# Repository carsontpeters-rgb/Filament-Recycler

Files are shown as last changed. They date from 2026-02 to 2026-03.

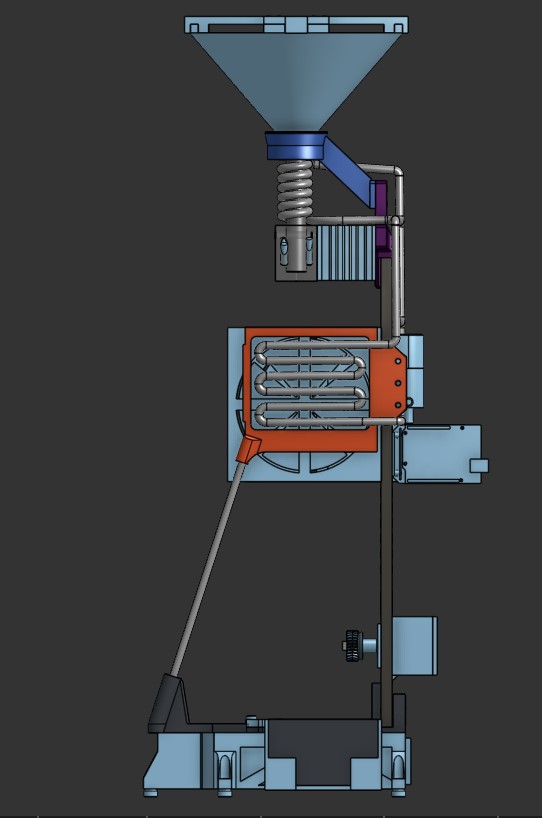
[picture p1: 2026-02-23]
Pictures/Assembly 3.jpg

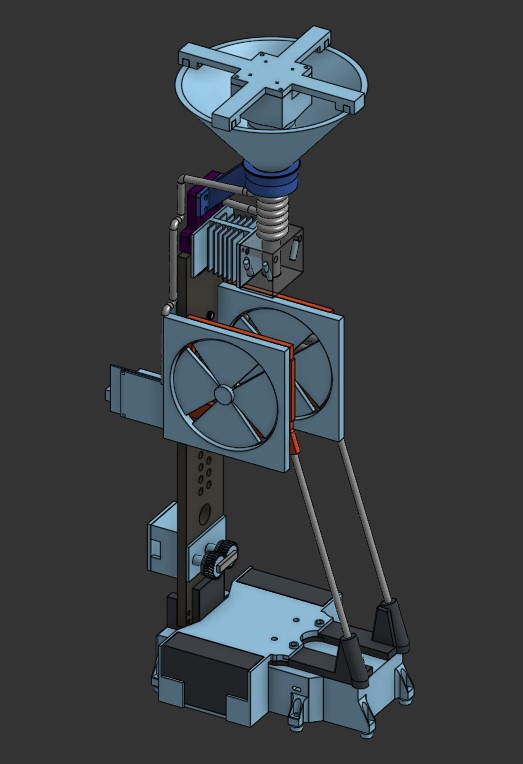
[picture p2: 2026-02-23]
Pictures/Assembly 1.jpg

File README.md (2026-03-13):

PLA Filament Recycler & Extruder
I got tired of throwing away failed prints and scraps of PLA, so I designed a machine that can recycle those scraps and turn them back into usable filament. You can also use raw PLA pellets as a material, which is much cheaper than buying a spool. Everything was designed from scratch, including the CAD, electronics, and code.
What it does
The machine takes in shredded 3D print scraps or raw PLA pellets, melts them down, and extrudes new 1.75mm filament. You can use this to recycle failed prints or support material and turn them back into usable filament. I designed this machine to save money and reduce waste from scraps of PLA I had already paid for.
How to use it

Shred old prints into small chips, or better yet, just use raw pellets. Put these into the top funnel.
Plug it in and it will automatically heat up to 210°C.
The plastic is pushed through a water-cooled steel barrel by an auger into the hot end. Melted plastic is pushed out through a 1.72mm nozzle.
Two 120mm fans cool the filament just after it exits the nozzle.
It is cooled again on its way to the spool via a stepper-driven puller, which regulates the filament diameter.
Spool it up by hand.

How it works
Feeding
Plastic goes into a hopper and gets pushed through a steel barrel by an auger. The barrel is water-cooled so that the plastic frame won't melt.
Heating
The hot end has two 12V cartridge heaters sitting in a custom-made heater block. Temperatures are monitored in real time by K-type thermocouples, which the firmware uses to maintain a constant 210°C.
Cooling & Diameter
The filament is rapidly cooled by two 120mm fans directly after exiting the nozzle. The stepper puller controls the filament diameter by varying the speed at which it pulls the filament away from the nozzle — the faster it pulls, the thinner the filament gets. You then spool it up by hand.

CAD File Notes
In the CAD file there are folders named parts, electronics, and non-printed parts. The parts folder contains everything I'll be 3D printing. The electronics folder has STEP files of all the electronics. The non-printed parts I'll either fabricate myself, have CNC'd, or purchase. Here is the link to the OnShape file https://cad.onshape.com/documents/712a637f79dd720bf38c4e9e/w/a795a65476a95b8c58273d13/e/a84f1c8939a0f9925b142090
the code was uploded using arduino ide to a arduino uno r3

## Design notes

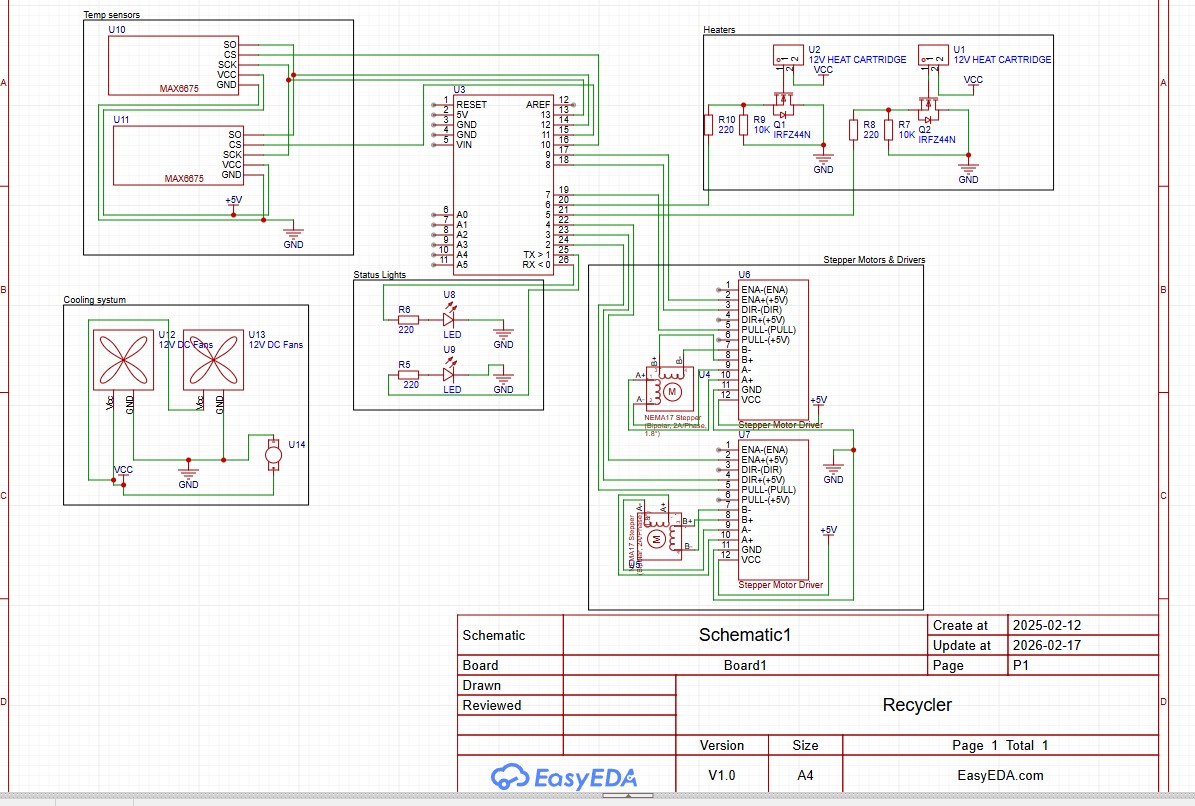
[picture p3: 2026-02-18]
Pictures/Schematic.jpg

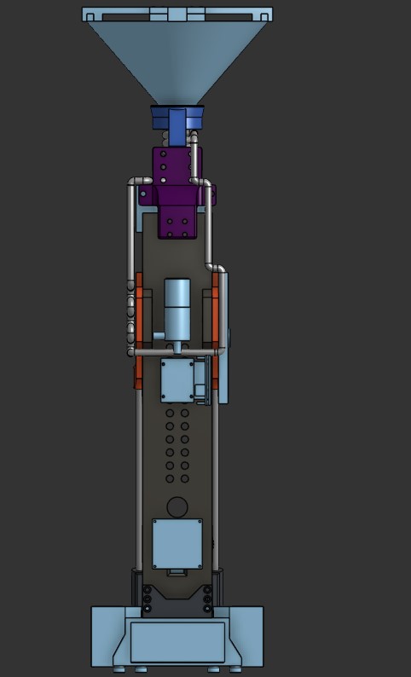
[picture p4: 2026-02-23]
Pictures/Screenshot 2026-02-23 073450.jpg

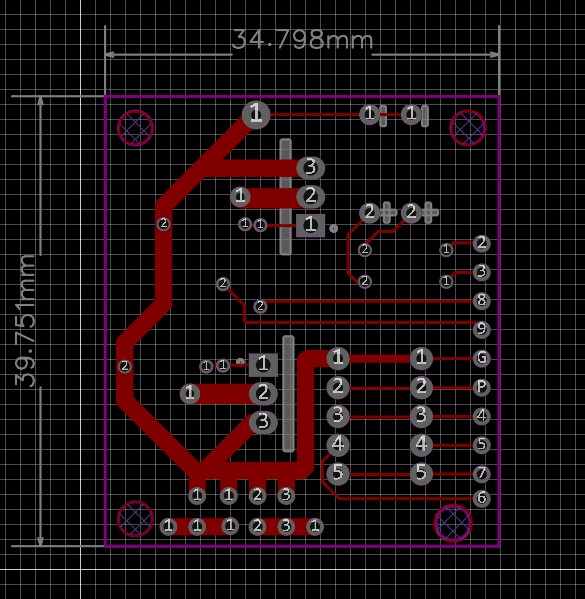
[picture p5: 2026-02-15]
Pictures/PCB.jpg

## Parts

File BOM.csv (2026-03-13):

Item Name | Description | Quantity | Unit Price | Total Price | URL | Total with tax
120mm Fan | Cooling fan for radiator | 2 | $9.89 | $19.78 | https://www.amazon.ca/gp/product/B002YFP8BK/ref=ox_sc_act_image_5?smid=A1W36NGWLHYVQ3 | $21.15
304 Stainless steel Pipe | Feed neck | 1 | $35.22 | $35.22 | https://www.amazon.ca/gp/product/B0CWY62TWC/ref=ox_sc_act_image_2?smid=A2NJO87SRDLPUU&psc=1 | $39.45
6mm Steel rod | Structual support rods | 1 | $6.79 | $6.79 | https://www.amazon.ca/gp/product/B0BDZ2VSCC/ref=ox_sc_act_image_3?smid=A2U2IW4XM8RL4X&psc=1 | $7.60
AC 110V - 220V TO DC | Power Supply | 1 | $20.95 | $20.95 | https://www.amazon.ca/gp/product/B010CVIWBK/ref=ewc_pr_img_1?smid=A2Z1VP11ZHYN88&psc=1 | $23.46
Aluminum SSR Heatsink | Heatsink | 1 | $13.49 | $13.49 | https://www.amazon.ca/gp/product/B07B3Y2ZNY/ref=ox_sc_act_image_8?smid=A35AFW9EVJYR0N&psc=1 | $15.11
Auger Drill Bit | Feed Auger | 1 | $19.45 | $19.45 | https://www.amazon.ca/gp/product/B0FSYZNZVQ/ref=ox_sc_act_image_12?smid=A2Y9NNYJ4PYMHW | $21.78
Copper round tube | For watercooling system | 1 | $15.69 | $15.69 | https://www.amazon.ca/gp/product/B09MK7HR1V/ref=ox_sc_act_image_1?smid=A30WUG2ZDGM0XM&psc=1 | $17.57
High Temperature Polyimide Tape | Heat shielding tape | 1 | $14.99 | $14.99 | https://www.amazon.ca/gp/product/B0D979ZV7G/ref=ox_sc_act_image_11?smid=ABKR4BJYL11O&psc=1 | $16.79
IRFZ44N Mosfets | Mosfets | 1 | $3.11 | $6.22 | https://www.amazon.ca/gp/product/B07PKDV4JH/ref=ox_sc_act_image_4?smid=A14A2SS3D2OXQ9&psc=1 | $6.97
MAX6675 Module | Heat sensors | 2 | $4.75 | $9.49 | https://www.amazon.ca/gp/product/B0C6QTL5Y3/ref=ox_sc_act_image_6?smid=A1VTL661FOEJB1&psc=1 | $10.63
NEMA17 Stepper Motor | Stepper motors | 2 | $9.00 | $18.00 | https://www.amazon.ca/gp/product/B0B1Q4CF87/ref=ox_sc_act_image_9?smid=A2GRTMR8P2IKL2&psc=1 | $20.16
Power Cord | cable to plug the psu in | 1 | $5.99 | $5.99 | https://www.amazon.ca/gp/product/B07BQCMPF2/ref=ox_sc_act_image_7?smid=A3DWYIK6Y9EEQB | $6.71
TB6600 Stepper Motor Driver | Stepper motor drivers | 2 | $21.36 | $42.72 | https://www.amazon.ca/gp/product/B07Z4YQ7CY/ref=ox_sc_act_image_10?smid=A22JVY9MHCKXI0&psc=1 | $47.85
Arduino Uno R3 | Micro Controller | 1 | $21.99 | $21.99 | https://www.amazon.ca/Elegoo-Board-ATmega328P-ATMEGA16U2-Arduino/dp/B01EWOE0UU?s=industrial | $24.63
Led | Lights | 2 | $2.19 | $4.38 | https://www.amazon.ca/Novelty-Place-Colors-Yellow-Lights/dp/B086V2M2TT/ref=sr_1_8?sr=8-8 | $4.91
Resitors | resitors | 6 | $0.02 | $0.12 | https://www.amazon.ca/Resistor-Assorted-Resistors-Assortment-Experiments/dp/B07L851T3V | $0.13
22 awg wire | wires | 1 | $22.98 | $22.98 | https://www.amazon.ca/Silicone-Electrical-Conductor-Parallel-Flexible/dp/B07K9R9LBV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 | $25.74
Totals with all parts |  |  | $227.85 | $278.25 |  | $310.64
Total of parts I need |  |  |  |  |  | $255.23
Cad to Usd convertion |  |  |  |  |  | $187.67

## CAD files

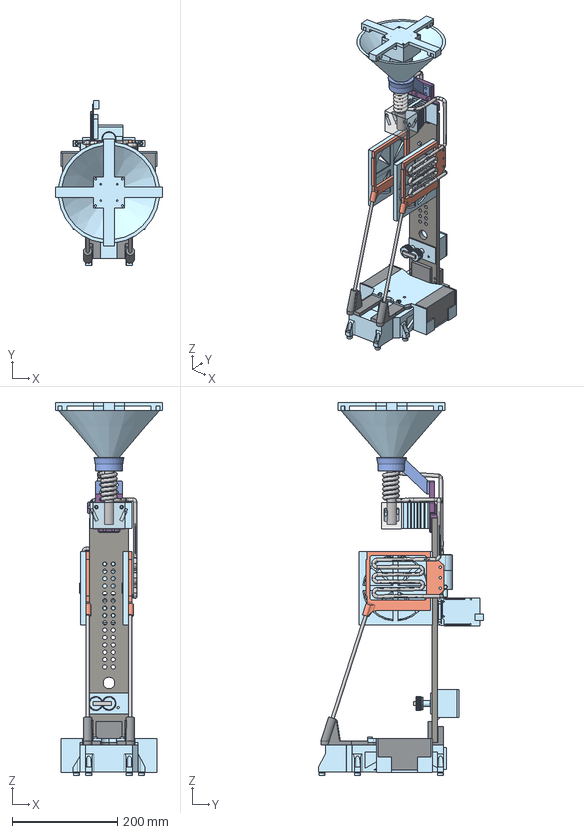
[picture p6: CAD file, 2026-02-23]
CAD/Assembly 1.step
203.2 x 313.6 x 709.5 mm
Spur gear (25 teeth) x 2

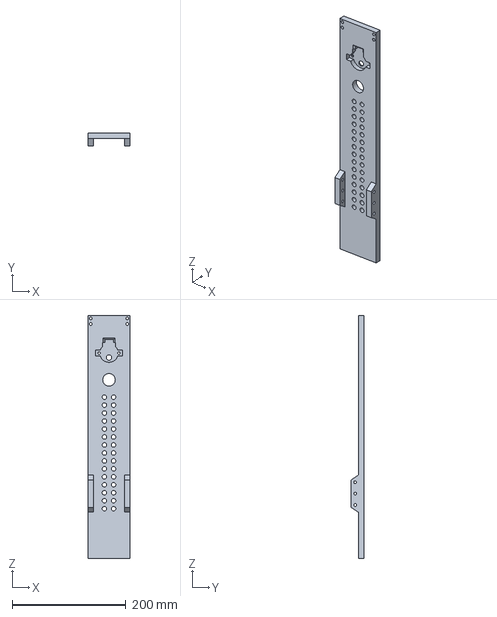
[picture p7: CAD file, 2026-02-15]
CAD/Parts/Main housing.step
74.0 x 23.0 x 427.0 mm

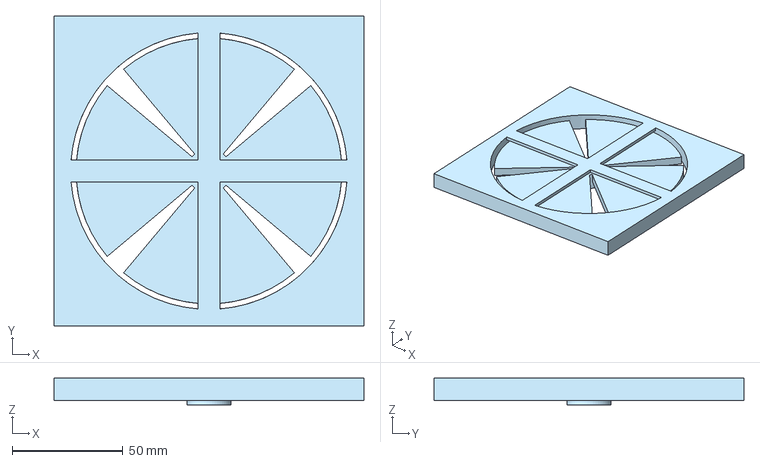
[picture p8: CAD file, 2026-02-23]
CAD/Electronics/Fans.step
140.0 x 140.0 x 12.0 mm

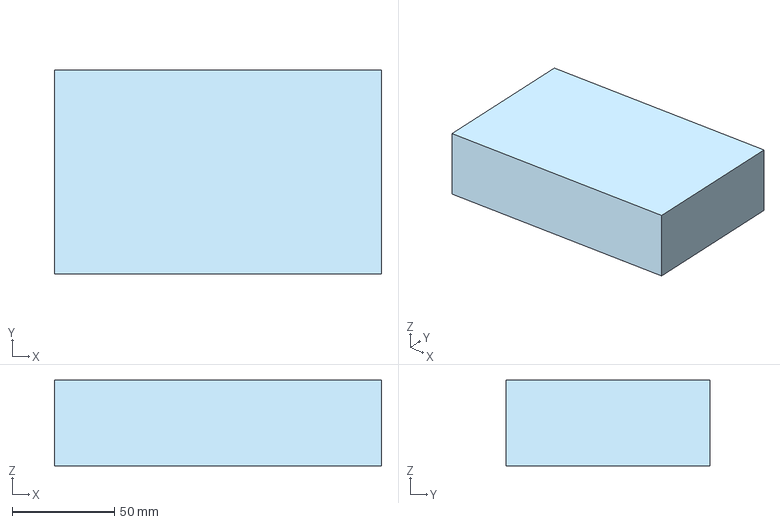
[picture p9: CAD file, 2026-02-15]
CAD/None 3D Printed Parts/psu.step
160.0 x 100.0 x 42.0 mm

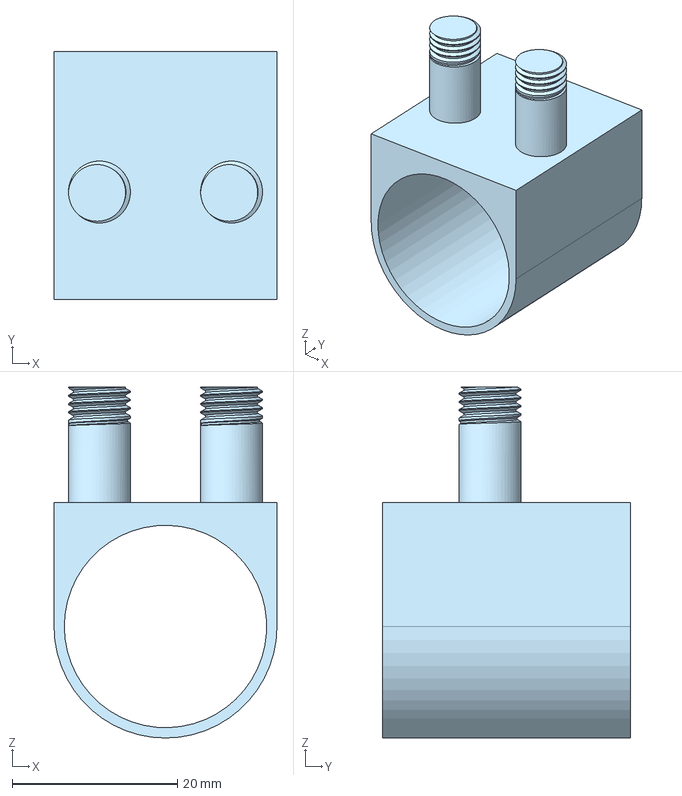
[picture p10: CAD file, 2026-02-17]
CAD/Parts/Pump Mount.step
27.0 x 30.0 x 42.5 mm

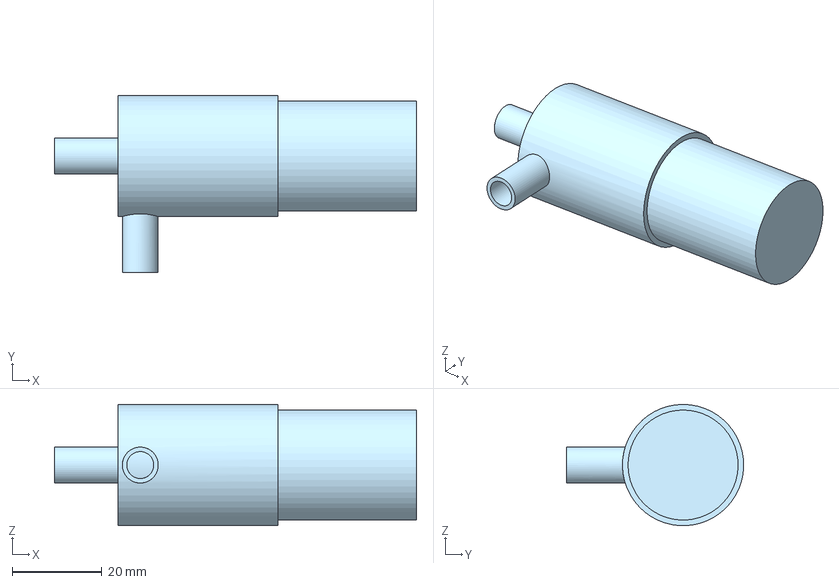
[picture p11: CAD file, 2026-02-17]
CAD/Electronics/Pump.step
80.6 x 39.5 x 27.0 mm

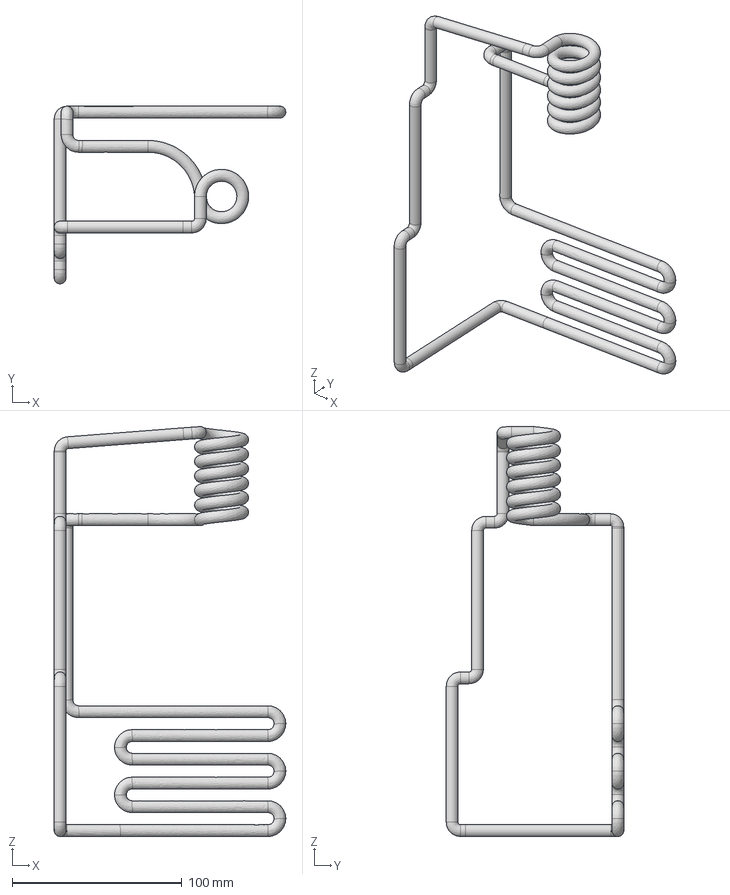
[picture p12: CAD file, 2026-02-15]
CAD/None 3D Printed Parts/Copper pipe.step
136.6 x 104.7 x 241.7 mm

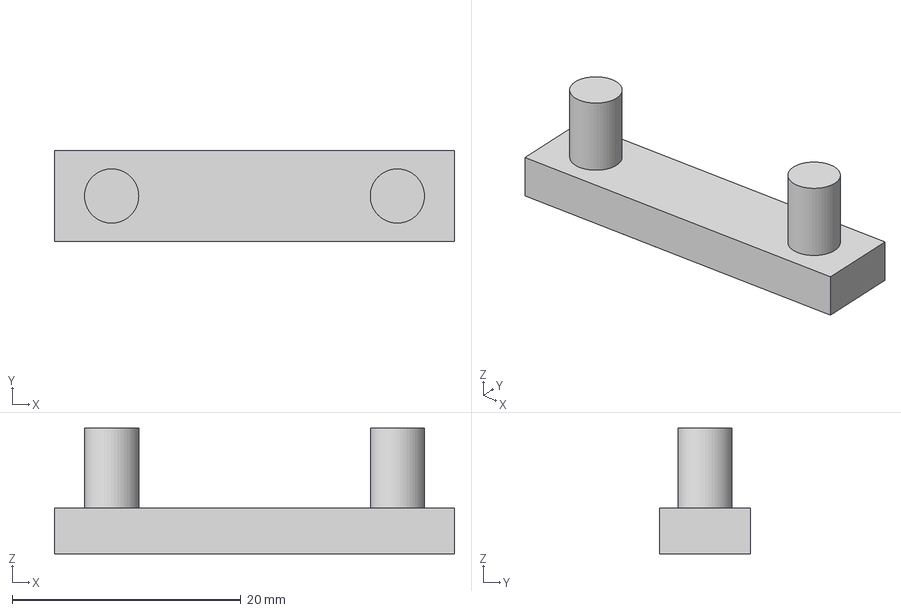
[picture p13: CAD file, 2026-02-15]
CAD/Parts/Gearbrace.step
35.0 x 8.00 x 11.0 mm

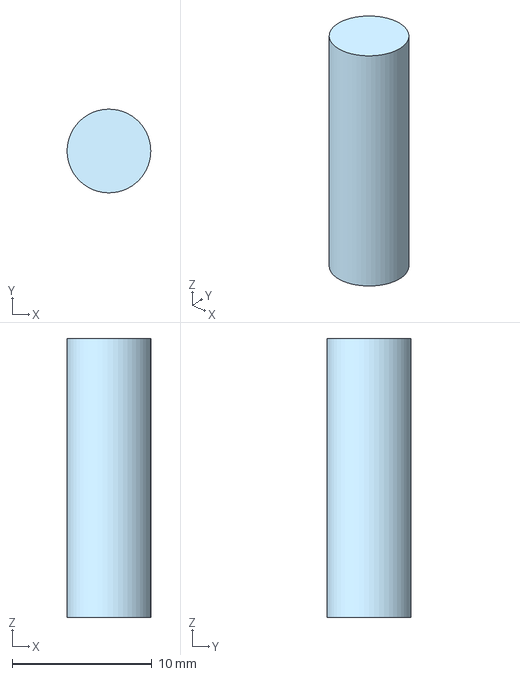
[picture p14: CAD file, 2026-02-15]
CAD/Electronics/Heaters.step
5.99 x 6.00 x 20.0 mm

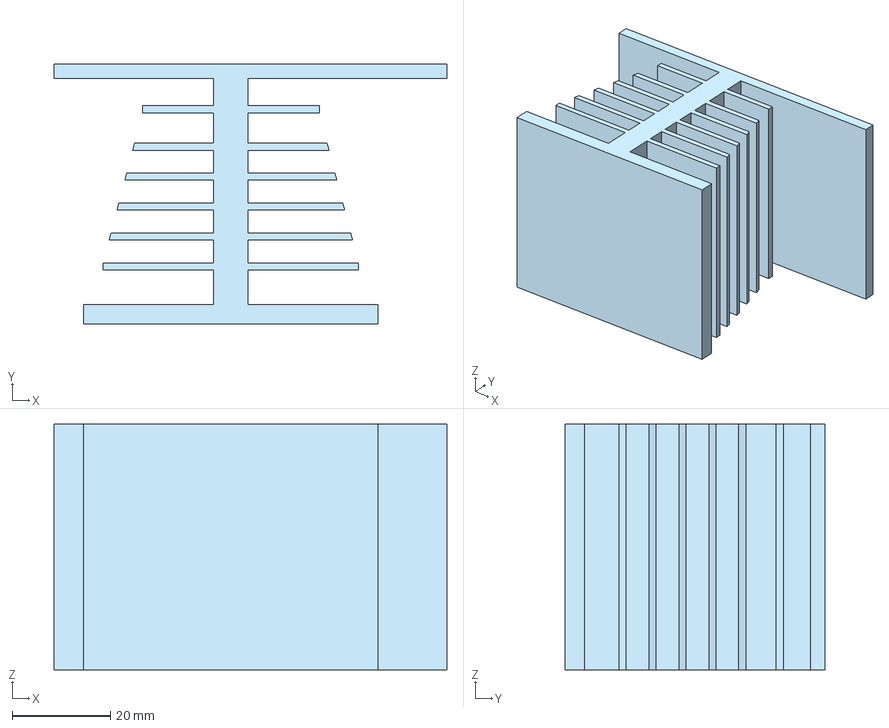
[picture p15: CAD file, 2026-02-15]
CAD/None 3D Printed Parts/Heatsink.step
80.0 x 53.0 x 50.0 mm

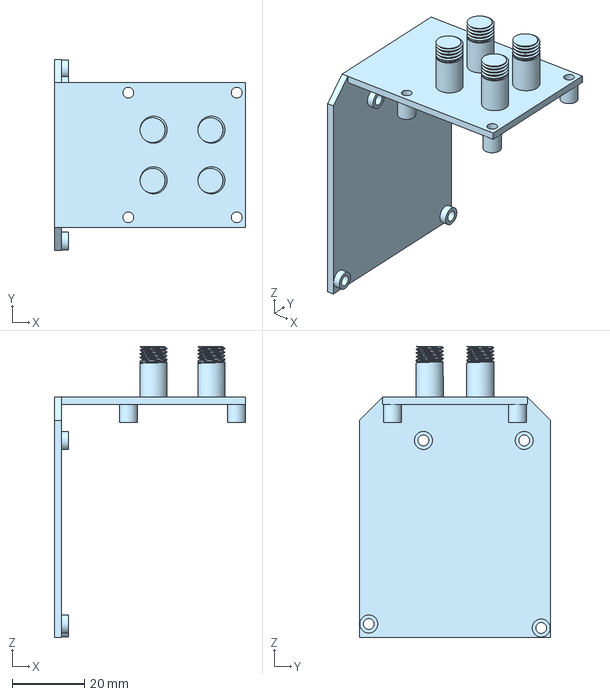
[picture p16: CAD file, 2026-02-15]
CAD/Parts/PCB Mount.step
53.0 x 53.0 x 80.5 mm

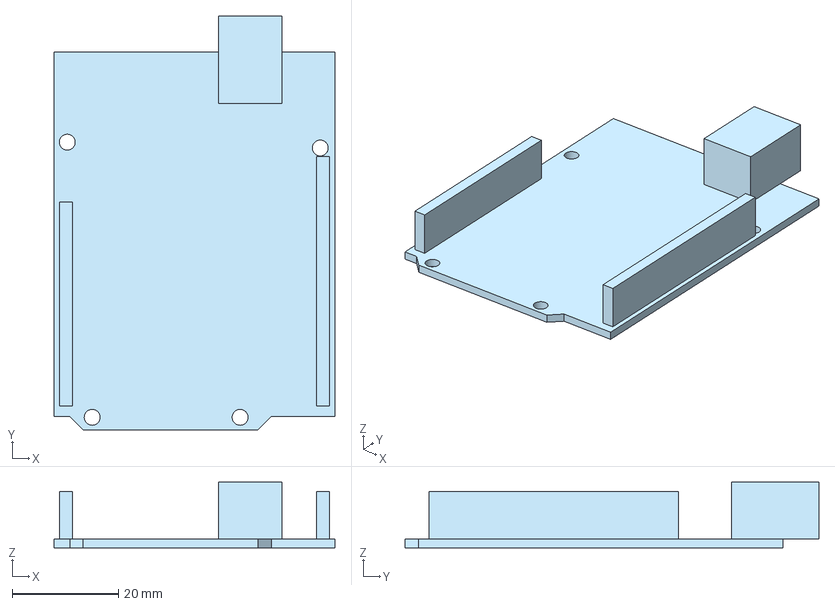
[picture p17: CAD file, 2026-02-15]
CAD/Electronics/Arduino.step
53.0 x 78.0 x 12.4 mm

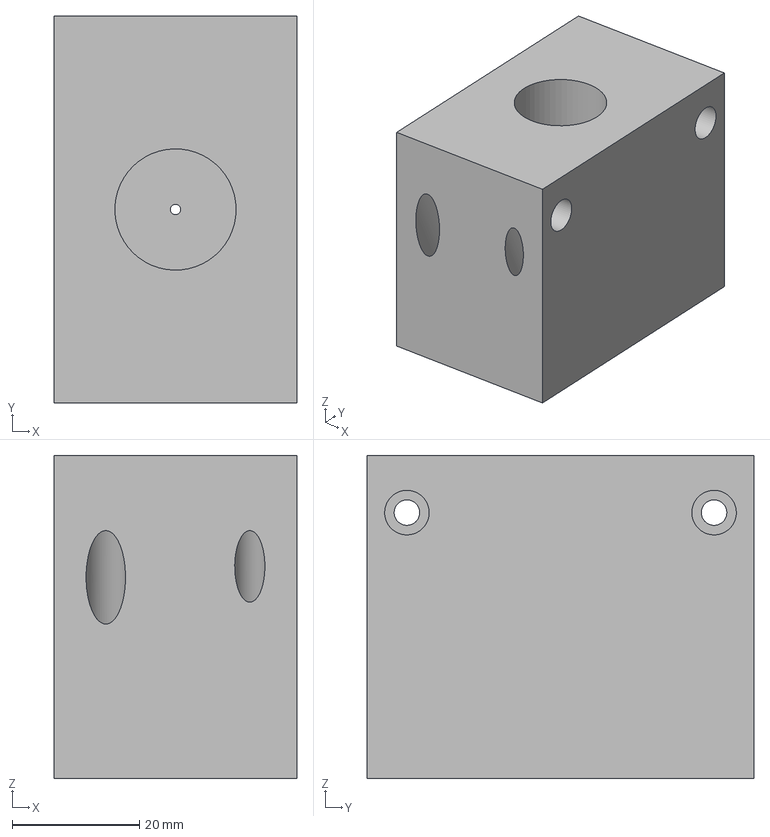
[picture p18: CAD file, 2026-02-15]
CAD/None 3D Printed Parts/Heating block.step
38.1 x 60.8 x 50.8 mm

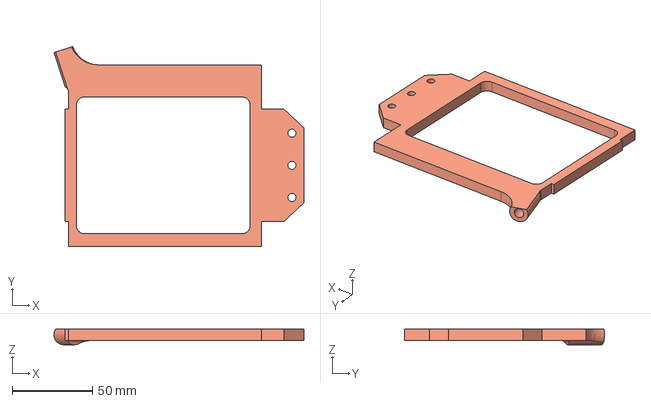
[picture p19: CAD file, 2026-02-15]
CAD/Parts/Fan bracket.step
155.5 x 124.4 x 9.67 mm

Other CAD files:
CAD/Electronics/Heat sensors.step
CAD/None 3D Printed Parts/rod.step
CAD/Parts/cone Bracket.step
CAD/Electronics/PCB.step
CAD/Electronics/Drivers.step
CAD/Electronics/Stepper Motors.step
CAD/None 3D Printed Parts/Steel Pipe.step
CAD/None 3D Printed Parts/spiral.step
CAD/Parts/Base plate.step
CAD/Parts/Connecter.step
CAD/Parts/Driver Mounts.step
CAD/Parts/Extender.step
CAD/Parts/Gear plate.step
CAD/Parts/M7.5x1 Nut.step
CAD/Parts/Motor Mount.step
CAD/Parts/PSU Connecters.step
CAD/Parts/PSU Housing Feet.step
CAD/Parts/Plantary gearbox.step
CAD/Parts/Psu Housing Back.step
CAD/Parts/Psu Housing.step
CAD/Parts/Puller Gear Output.step
CAD/Parts/Puller gear I.step
CAD/Parts/Stepper Motor Adapter.step
CAD/Parts/Stepper motor cover.step
CAD/Parts/cone.step

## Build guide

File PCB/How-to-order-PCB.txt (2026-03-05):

How to Order PCB

Please refer to:
https://prodocs.easyeda.com/en/pcb/order-order-pcb/index.html

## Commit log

2026-02-15 Create Stl
2026-02-15 Create None 3D Printed Parts
2026-02-16 Update and rename BOM - Sheet1.csv to BOM.csv
    [BOM.csv]
2026-02-23 Rename Screenshot 2026-02-23 073430.jpg to Assembly 1
2026-02-23 Rename Screenshot 2026-02-23 073450.jpg to Assembly 2
2026-02-23 Rename Screenshot 2026-02-23 073502.jpg to Assembly 3
2026-02-23 Clarify CAD file labels in README
    Updated the README to clarify the labeling of CAD files and added details about 3D printed parts.
2026-03-05 Revise README for PLA Filament Recycler & Extruder
    Updated the README to provide a clearer explanation of the PLA Filament Recycler & Extruder, including its functionality, usage instructions, and detailed workings.
2026-03-06 Update README with CAD file information and link
    Added details about CAD files and links to Onshape.
2026-03-13 Initialize heater and motor control with PID
2026-03-13 Fix spelling and formatting in BOM.csv
    Updated BOM.csv to correct spelling errors and formatting issues.
    [BOM.csv]
2026-03-13 Update Arduino model in README.md
